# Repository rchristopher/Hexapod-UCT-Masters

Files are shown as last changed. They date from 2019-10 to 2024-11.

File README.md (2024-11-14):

# Hexapod-UCT-Masters
Hexapod project for MSc. Eng. at The University of Cape Town

#### C++ hexapod code documentation
https://rchristopher.github.io/Hexapod-UCT-Masters/

#### Final report
https://drive.google.com/file/d/1L6Y8xdj6XzMt_z8zyFrfKeZr-7HOm_jE

#### Videos of the hexapod in operation can be found at:

Hexapod Twisting its Body: https://youtu.be/Y7dhTmXj7jc

Hexapod Height Changing: https://youtu.be/q2x5ghlYeB8

Hexapod on Charging Base: https://youtu.be/d-ti27CiAhU

Hexapod Walking at Speed: https://youtu.be/vn0S7XvKXdE

Hexapod Walking on Slope: https://youtu.be/eth4lNTiyJM

Hexapod Walking with Height Changes: https://youtu.be/5solkBVhNds

Research Expo Poster

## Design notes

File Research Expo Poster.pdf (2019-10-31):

# Introduction

# Mathematical Modelling and Control System Optimization of a Hexapod Robot

## Ross Christopher Supervised by A/Prof Hennie Mouton Robotics and Agents Research Lab University of Cape Town

# Controller and Peripherals

# Mathematical Modelling

The work done in this project aims to improve the hexapod that has been developed in The University of
Cape Town’s Robotics and
Agents Research Lab, by
implementing an effective control algorithm such that the
robot can move with a
high degree of agility and precision.

The hexapod is designed to be used in search and rescue applications due to its advanced mobility.

Mathematical modelling of the robot was essential in order to develop an algorithm to achieve a smooth walking motion.

The forward kinematics of one leg was calculated using Denavit-Hartenberg notation [1] to assign coordinate systems to each joint of the leg. Using these coordinate systems a rotation matrix representing the forward kinematics was developed.

The leg joint angles were related to the foot XYZ position using inverse kinematics [2]. This was calculated with trigonometry as shown in figure 2 below.

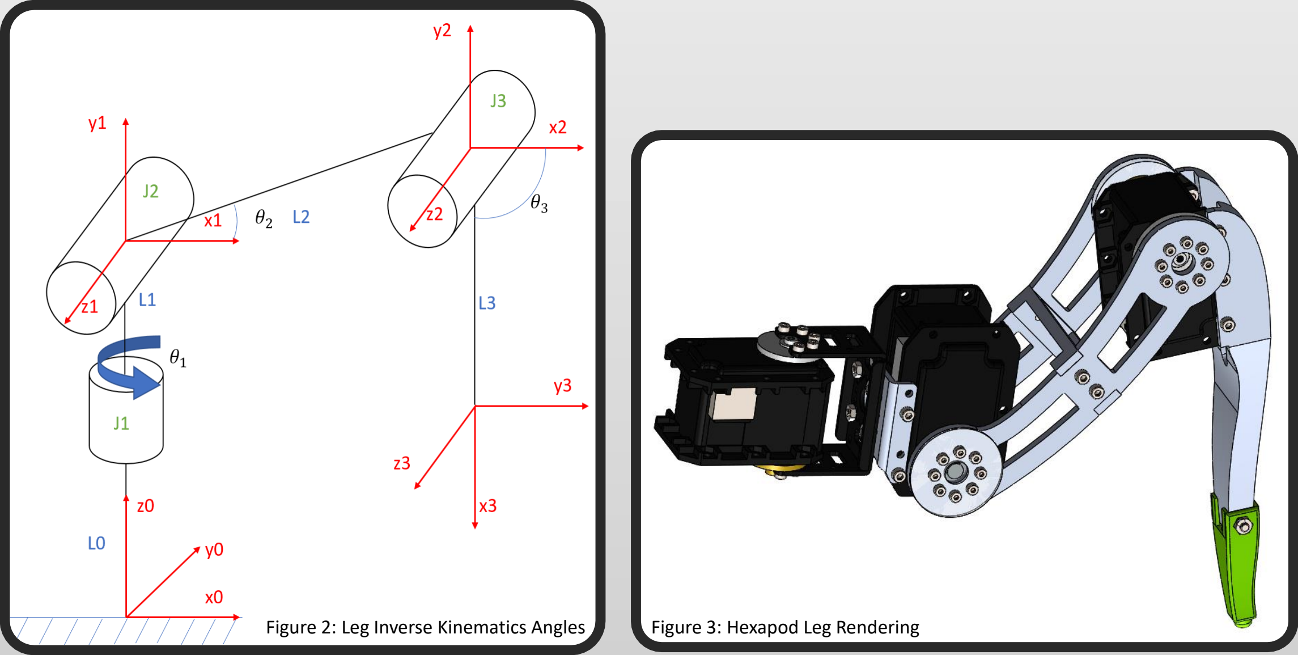
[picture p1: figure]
Figure 2: Leg Inverse Kinematics Angles; Figure 3: Hexapod Leg Rendering

This facilitated the creation of an algorithm for individual leg position control. Kinematics relating the hexapod body position to the foot position of each leg was developed.

A dynamic model for the leg was then developed using Lagrangian dynamics [3]. This model defines the relationship between joint torques and foot forces which can be used in gripping and friction force calculations.

Trajectory generation was used to generate a third order polynomial path [4] of motion for each leg; made up of the swing phase (where the leg is moving through the air) and the support phase (where the leg is touching the ground).

The hexapod includes a central microcontroller, a wireless transmitter for remote control and an accelerometer module.

An ARM microcontroller is used as the main controller of the hexapod; programmed in object orientated C++. This allows for an instant startup time of the hexapod and fast processing of commands [5]. The controller calculates the inverse kinematics of each path point, for all legs, in real time and sends this data to all 18 Dynamixel motors via serial communication.

This allows for the implementation of adaptive walking as all calculations can be adjusted and updated, in real time, as the hexapod moves.

The wireless transmitter is an RF1100-232 module. It transmits serial data between the hexapod and a computer at a speed of 433MHz. This data includes position and orientation commands from the computer and feedback signals (such as motor temperatures and torques) from the hexapod.

The accelerometer module is an XSens Mti-28A. It allows for accurate position and orientation measurement in 3 axes. These measurements are fed into a PID [6] controller which allows the orientation of the hexapod to be set and maintained. Currently the Hexapod is set to maintain a level body even if the ground is not level.

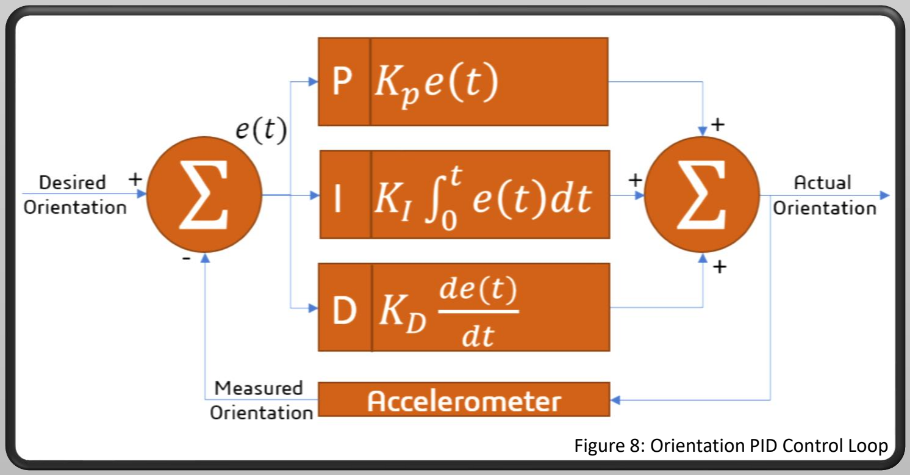
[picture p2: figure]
Figure 8: Orientation PID Control Loop

# References

### Kinematics and Dynamics

### Leg Trajectory Generation

This allows for a smooth motion when moving the foot between points as seen in the position plot in figure 4.

A tripod walking motion was achieved by moving each leg through the points in their respective paths.

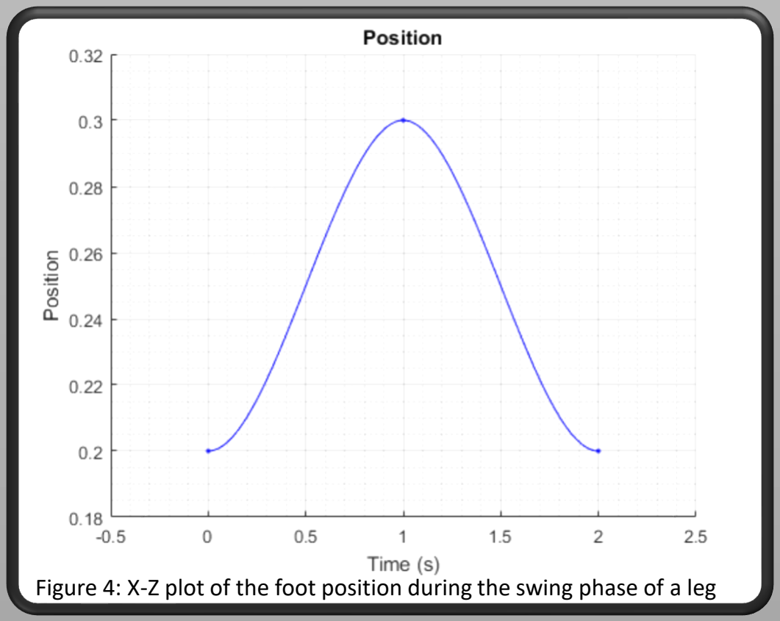
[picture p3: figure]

Figure 4: X-Z plot of the foot position during the swing phase of a leg

### STM32F4 Microcontroller

### Wireless Transmitter

Figure 6: RF1100-232 Wireless Module

Figure 5: STM32 Microcontroller Communicating with Dynamixel Motor

### Accelerometer

Figure 7: XSens Mti-28A Accelerometer

[1] A. P. Gracia, "Kinematics of Robots," 2007.
[2] M. M. U. A. a. M. A. R. Ahad, "Inverse Kinematics Solution for a 3DOF Robotic Structure using Denavit-Hartenberg Convention," 2014.
[3] T. Jintanawan, "Advanced Dynamics," 2005.
[4] C. S. Gurel, "Hexapod Modelling, Path Planning, and Control," The University of Manchester, 2017.
[5] A. Ahmed et al., "A Miniature Legged Hexapod Robot Controlled by a FPGA," International Journal of Mechanical Engineering and Mechatronics, vol. 1, no. 2, 2013.
[6] O. Aydogdu and M. Korkmaz, "A Simple Approach to Design of Variable Parameter PID controller," presented at the International Conference on Advancements in Information Technology, Singapore, 2011.

Figure 1: Hexapod Robot

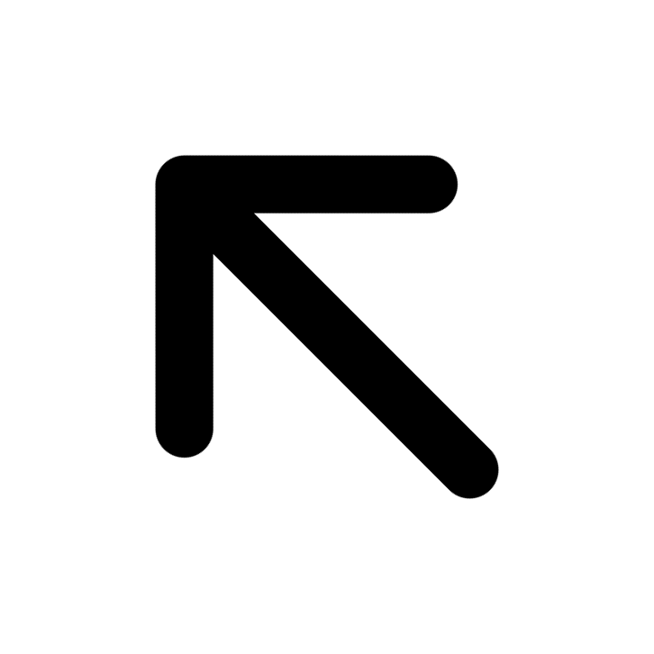
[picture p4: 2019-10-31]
Hexapod Control GUI/src/images/arrows/left_up.png

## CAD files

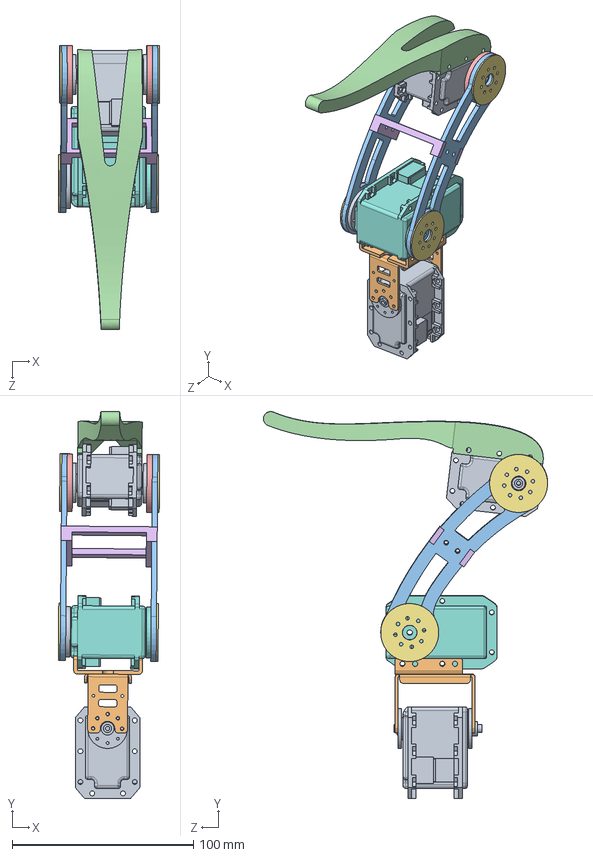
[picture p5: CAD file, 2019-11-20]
Solidworks/Assembly-Leg_no_foot.SLDASM
56.0 x 213.5 x 156.8 mm
RX-28Dual x 2
Std Part - Bracket
Leg - Femur-large x 2
Leg - Tibia - machined_no_foot
Leg - Spacer - 3mm x 2
Leg - Femur Support Bracket (large)
Leg - Spacer x 4
rx64N
RX64 bearing horn-outer
RX64 bracket (2018 new)

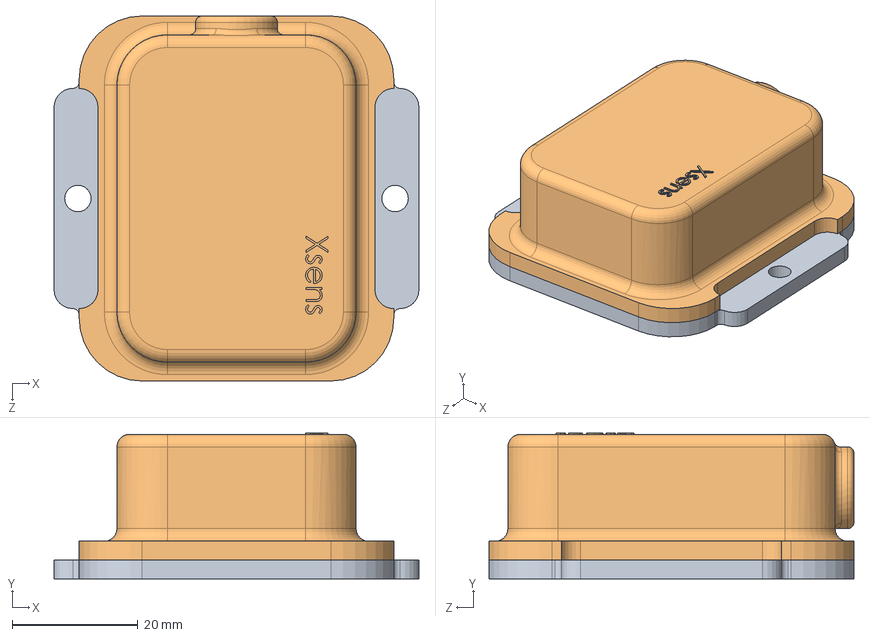
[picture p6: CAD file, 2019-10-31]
Solidworks/Xsens MTI-28/Assem8.SLDASM
58.0 x 23.2 x 58.0 mm
Base
Top

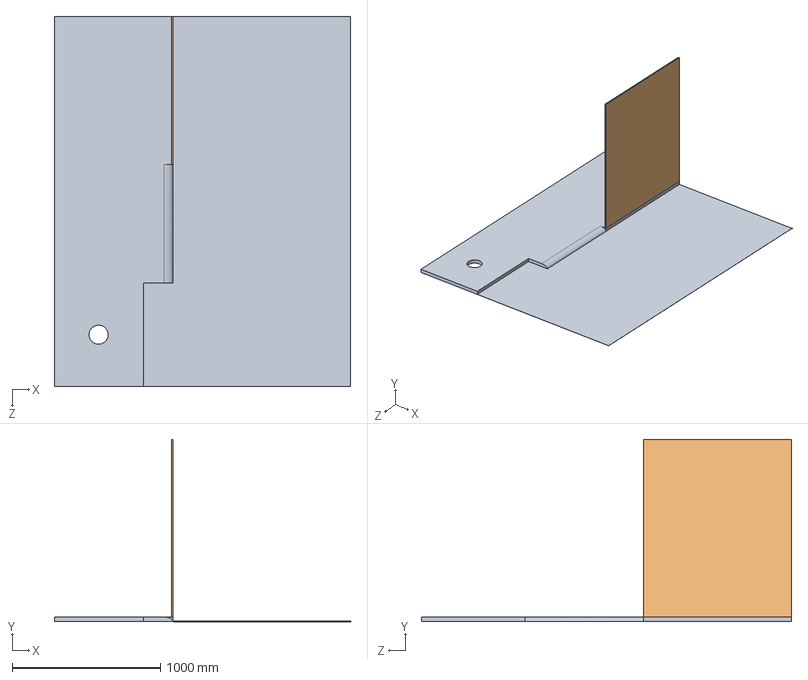
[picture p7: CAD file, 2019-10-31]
Solidworks/Assem1.SLDASM
2000.0 x 1231.0 x 2500.0 mm
Part1^Assem1
Part3^Assem1

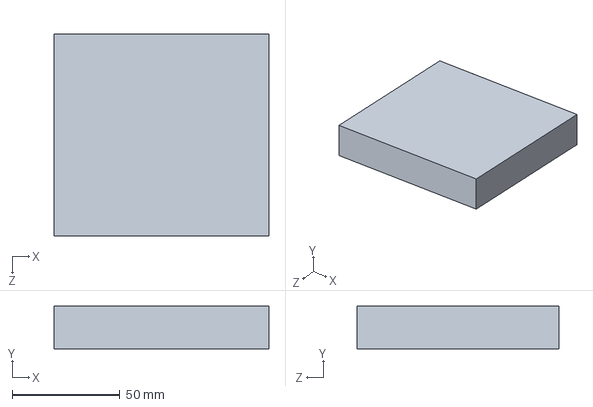
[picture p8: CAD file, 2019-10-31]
Solidworks/Circuit Boards/main prototype board.SLDPRT
100.0 x 20.0 x 94.0 mm

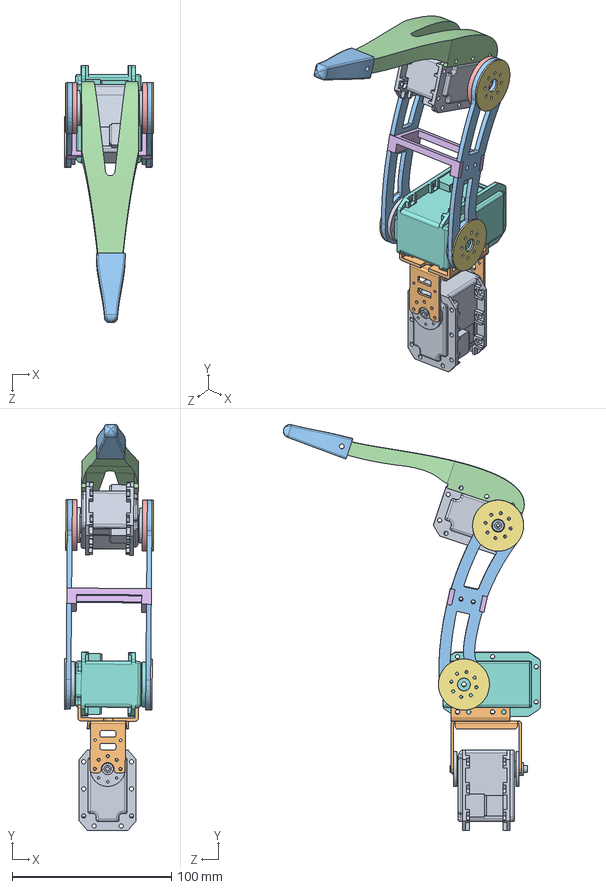
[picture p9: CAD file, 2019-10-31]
Solidworks/Assembly-Leg.SLDASM
56.1 x 254.6 x 161.3 mm
RX-28Dual x 2
Std Part - Bracket
Leg - Femur-large x 2
Leg - Tibia - machined
Leg - Spacer - 3mm x 2
Leg - Femur Support Bracket (large)
Leg - Spacer x 4
rx64N
RX64 bearing horn-outer
RX64 bracket (2018 new)
Foot_Solid_2018

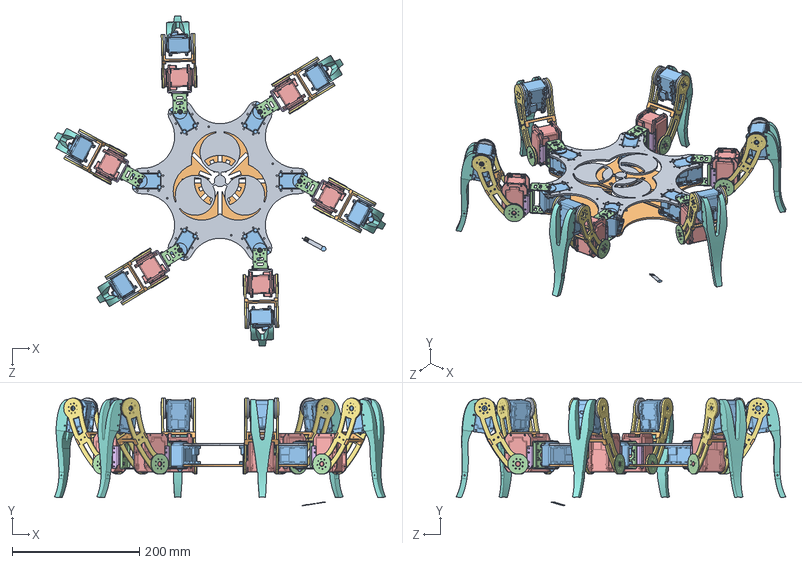
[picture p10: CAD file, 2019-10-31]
Solidworks/Assem2.SLDASM
520.1 x 169.2 x 518.3 mm
Base - Hex -upper
Base - Hex- lower
RX-28Dual x 12
Std Part - Bracket x 6
rx64H x 6
standard part - small bracket - rx64 x 6
Leg - Femur-large x 12
Leg - Tibia - machined x 6
Leg - Spacer - 2.5mm x 12
Leg - Femur Support Bracket (large) x 6
Leg - Spacer x 12

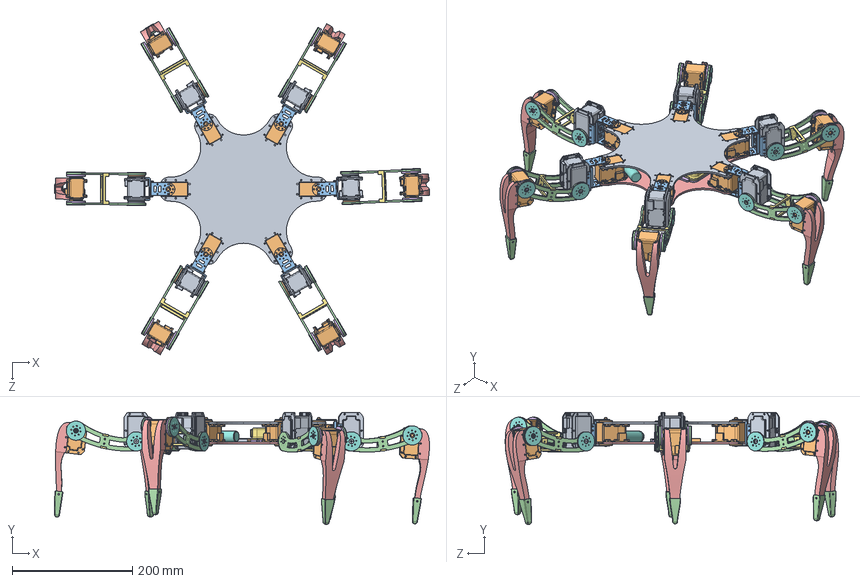
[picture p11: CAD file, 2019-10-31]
Solidworks/Assembly - Hex - 2019.SLDASM
624.0 x 186.5 x 555.0 mm
Base - Hex -upper
RX-28Dual x 12
Std Part - Bracket x 6
Leg - Femur-large x 12
Leg - Tibia - machined x 6
Leg - Spacer - 3mm x 12
Leg - Femur Support Bracket (large) x 6
Leg - Spacer x 23
rx64N x 6
RX64 bearing horn-outer x 6
RX64 bracket (2018 new) x 6
Foot_Solid_2018 x 6
Base - Hex- lower
PCB v1
remote

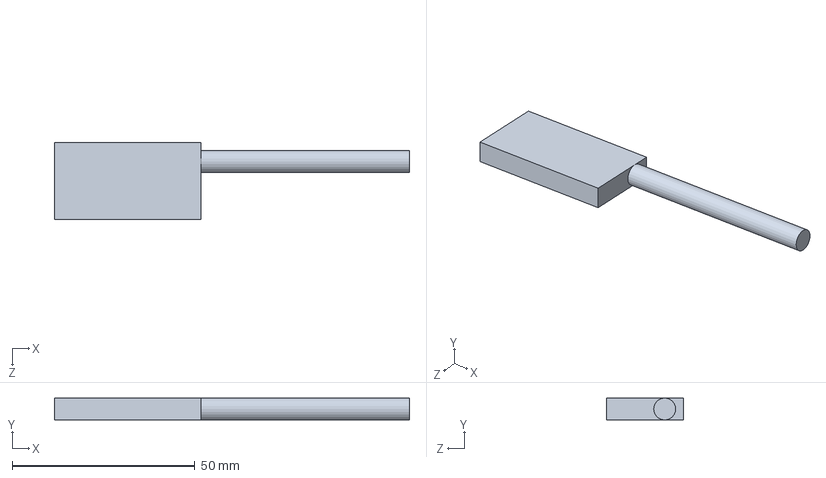
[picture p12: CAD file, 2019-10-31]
Solidworks/Circuit Boards/remote.SLDPRT
97.0 x 6.00 x 21.0 mm

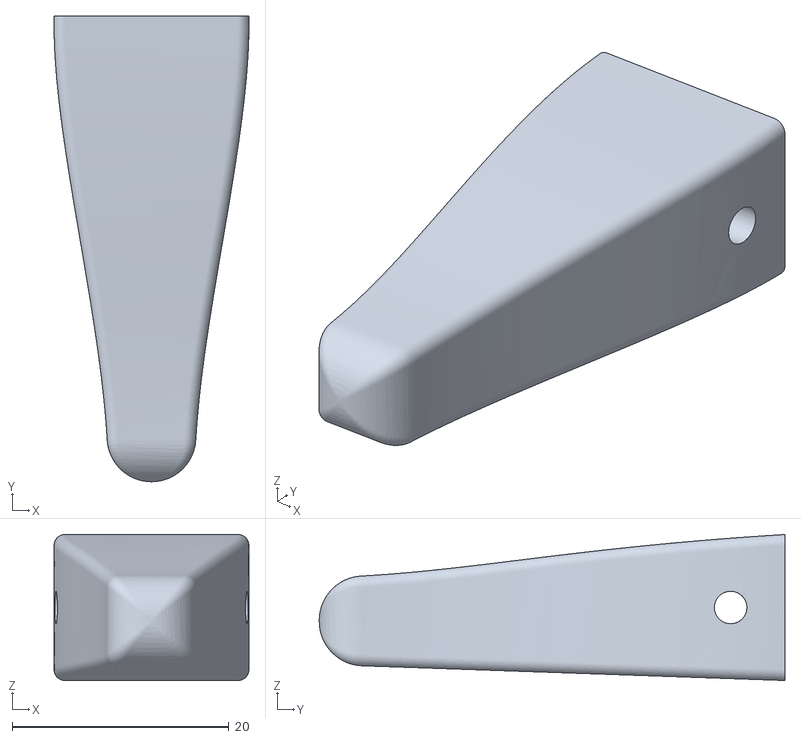
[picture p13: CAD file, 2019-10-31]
Solidworks/Parts to 3D print/Foot_Solid_2018_updated.STL
18.0 x 43.0 x 13.5

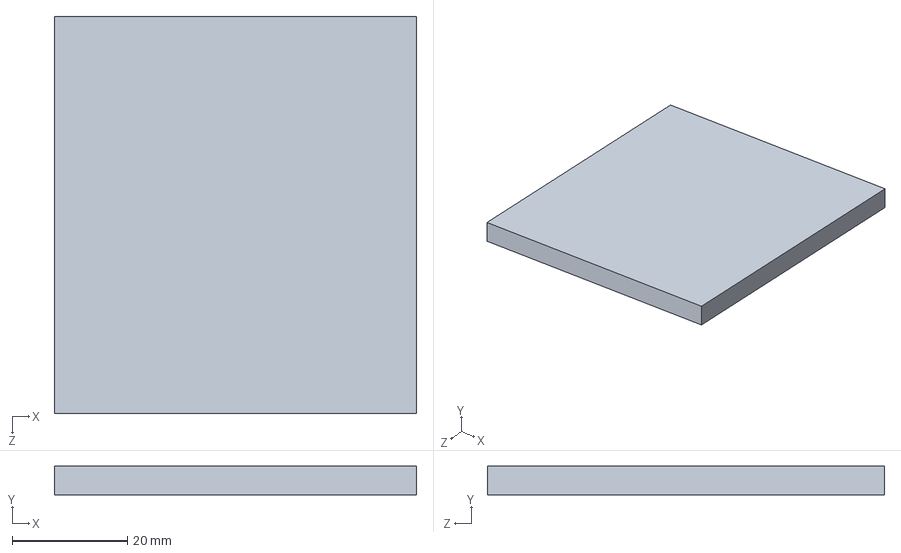
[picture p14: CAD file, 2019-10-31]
Solidworks/Circuit Boards/PCB v1.SLDPRT
63.0 x 5.00 x 69.0 mm

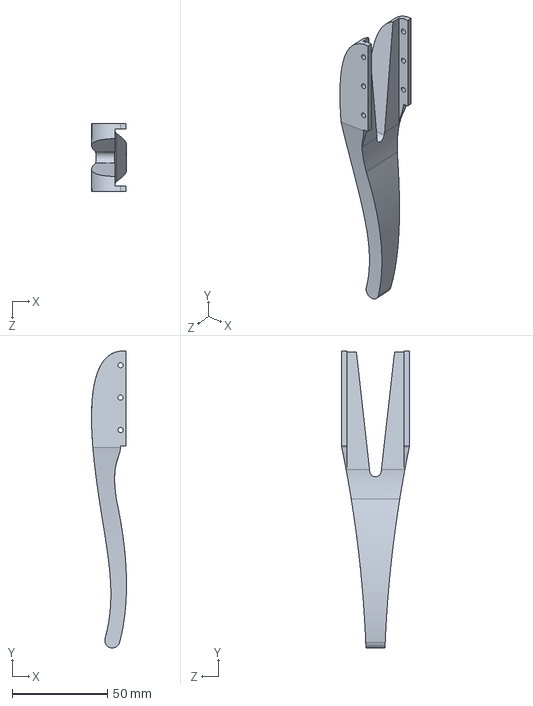
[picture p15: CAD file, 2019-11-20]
Solidworks/Leg - Tibia - machined_no_foot.SLDPRT
18.4 x 156.0 x 35.5 mm

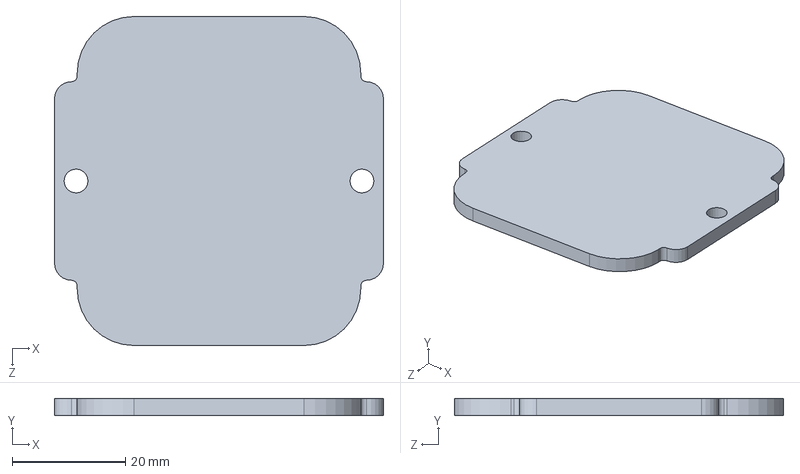
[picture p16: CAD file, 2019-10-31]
Solidworks/Xsens MTI-28/Base.SLDPRT
58.0 x 3.00 x 58.0 mm

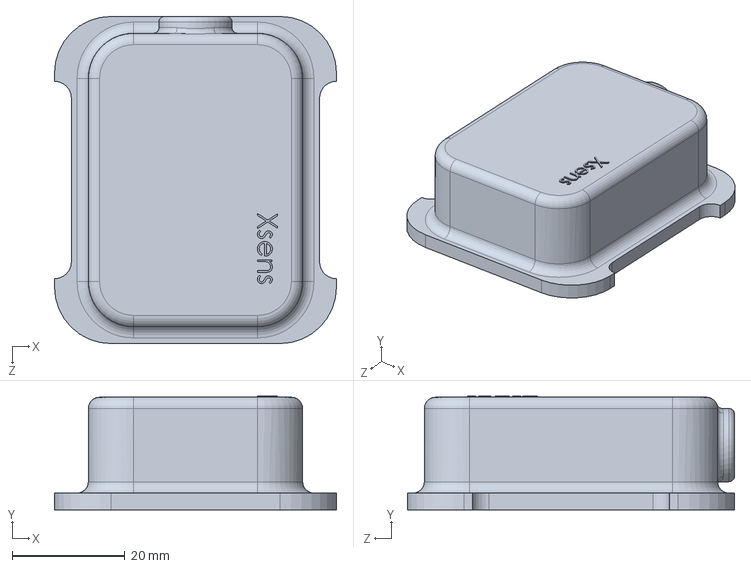
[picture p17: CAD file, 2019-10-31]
Solidworks/Xsens MTI-28/Top.SLDPRT
50.0 x 20.2 x 58.0 mm

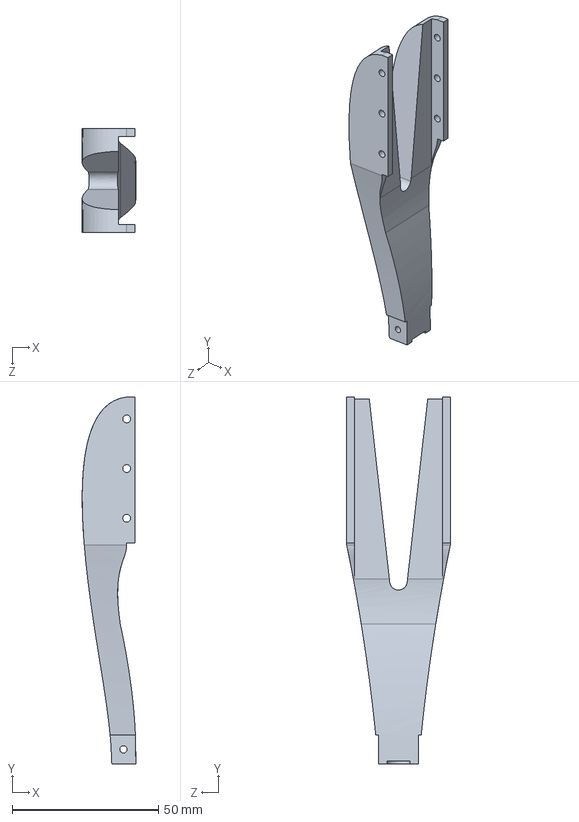
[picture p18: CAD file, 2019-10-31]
Solidworks/Leg - Tibia - machined.SLDPRT
18.4 x 125.6 x 35.5 mm

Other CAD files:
Solidworks/Std Part - Bracket.SLDPRT
Solidworks/RX-28Dual.SLDPRT
Solidworks/rx64H.SLDPRT
Solidworks/pc_mount_bar.SLDPRT
Solidworks/Assembly-Leg_old_motors.SLDASM
Solidworks/Base - Hex -upper .SLDPRT
Solidworks/Base - Hex- lower .SLDPRT
Solidworks/Circuit Protector Base.SLDPRT
Solidworks/Drawings/Protractor.SLDDRW
Solidworks/Drawings/RX64 bearing horn-outer.SLDDRW
Solidworks/Drawings/Top view base.SLDDRW
Solidworks/Drawings/rx64N_HORN.SLDDRW
Solidworks/Foot_Solid_2018.SLDPRT
Solidworks/Leg - Femur Support Bracket (large).SLDPRT
Solidworks/Leg - Femur Support Bracket.SLDPRT
Solidworks/Leg - Femur-large.SLDPRT
Solidworks/Leg - Spacer - 2.5mm (1).SLDPRT
Solidworks/Leg - Spacer - 2.5mm (2).SLDPRT
Solidworks/Leg - Spacer - 2.5mm (3).SLDPRT
Solidworks/Leg - Spacer - 2.5mm (4).SLDPRT
Solidworks/Leg - Spacer - 2.5mm.SLDPRT
Solidworks/Leg - Spacer - 3mm.SLDPRT
Solidworks/Leg - Spacer.SLDPRT
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

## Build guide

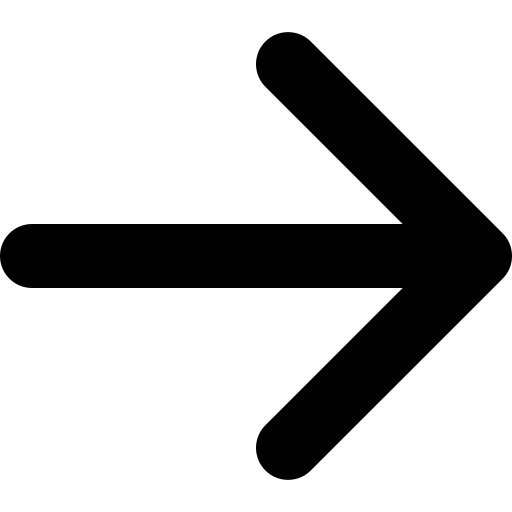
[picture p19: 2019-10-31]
Hexapod Control GUI/build/classes/images/arrows/right.png

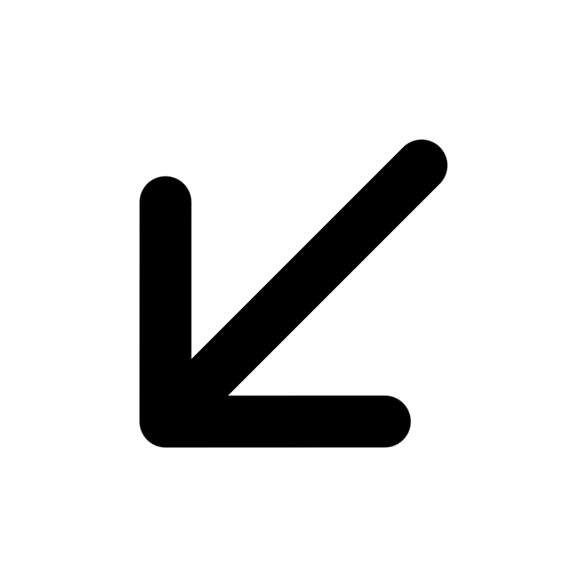
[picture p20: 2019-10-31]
Hexapod Control GUI/build/classes/images/arrows/left_down.png

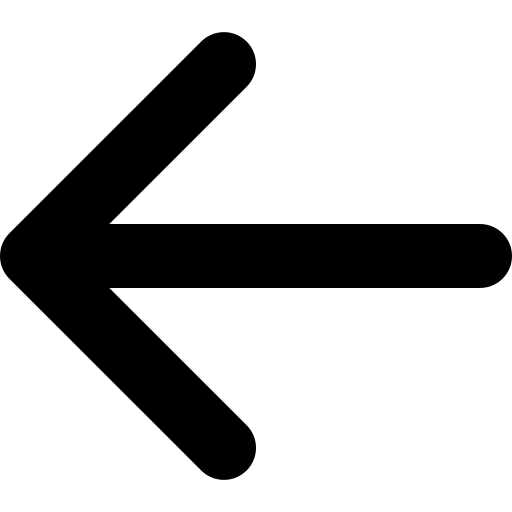
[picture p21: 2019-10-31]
Hexapod Control GUI/build/classes/images/arrows/left.png

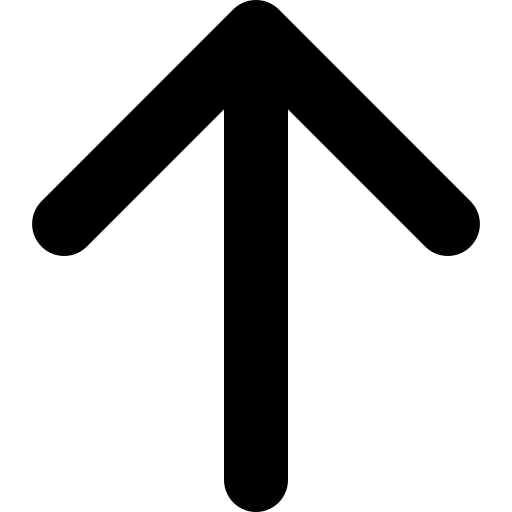
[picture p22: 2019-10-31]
Hexapod Control GUI/build/classes/images/arrows/up.png

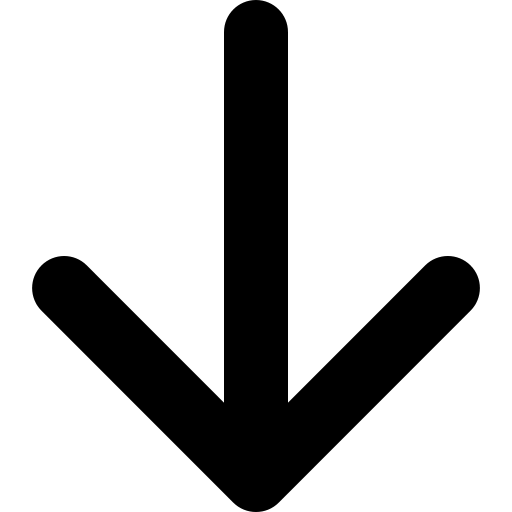
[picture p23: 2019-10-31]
Hexapod Control GUI/build/classes/images/arrows/down.png

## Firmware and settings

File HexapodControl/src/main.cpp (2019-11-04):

/**
 * @file main.cpp
 * @author Ross Christopher (CHRROS005)
 * @date
 * @brief main function
 **/

#include "CommsManager.h"
#include "Hexapod.h"

/** @brief Main Hexapod object.  **/
Hexapod HEX;

void main(){

	HEX.Initialise();
	HEX.startTimers();

	for(int i = 0; i < 1000000;i++);	//delay (HAL_Delay causes timer issues)
	HEX.stand();
	for(int i = 0; i < 100000;i++);	//delay (HAL_Delay causes timer issues)

	//HAL_Delay(5000);

	/*uint8_t data[] = {250};
	HEX.writeRegAll(RETURN_DELAY_TIME, data, 1);*/

	/*uint8_t data2[] = {32, 32};
	HEX.writeRegAll(CW_COMPLIANCE_SLOPE, data2, 2);*/

	HEX.pidPitch->togglePID(false);
	HEX.pidRoll->togglePID(false);
	HEX.pidYaw->togglePID(false);

	//HEX.pidPitch->setParameters(1,0,0);

	//uint8_t data3[] = {180,0,75,3};		//correct for motor 1 not hitting body.		// ALL IGNORING OTHER LEG POSITIONS
	//uint8_t data3[] = {75,0,245,3};		//correct for motor 2 not hitting body.
	//uint8_t data3[] = {0,0,190,3};		//correct for motor 3 not hitting body.
	/*for(int i = 0; i < 6; i++){			//change all legs
		HEX.legs[i]->motors[2]->writeReg(CW_ANGLE_LIMIT_L, data3, 4);
	}*/

	//HEX.liftOntoBase();

	HEX.timersReady = true;

	while(1){	//super loop


		/*HEX.legs[3]->setPosition(-243.710,0.0,-100);		// 1
		HEX.legs[3]->move();

		HEX.legs[3]->setPosition(-243.710,40.0,-100);	// 2
		HEX.legs[3]->move();

		HEX.legs[3]->setPosition(-243.710,-40.0,-100);	// 3
		HEX.legs[3]->move();

		HEX.legs[3]->setPosition(-283.710,0.0,-100);	// 4
		HEX.legs[3]->move();

		HEX.legs[3]->setPosition(-283.710,40.0,-100);	// 5
		HEX.legs[3]->move();

		HEX.legs[3]->setPosition(-283.710,-40.0,-100);	// 6
		HEX.legs[3]->move();

		HEX.legs[3]->setPosition(-203.710,0.0,-100);	// 7
		HEX.legs[3]->move();

		HEX.legs[3]->setPosition(-203.710,40.0,-100);	// 8
		HEX.legs[3]->move();

		HEX.legs[3]->setPosition(-203.710,-40.0,-100);	// 9
		HEX.legs[3]->move();*/

	/*	HEX.legs[3]->setPosition(-203.710,-80.0,-100);	// speed 0
		HEX.legs[3]->move();

		HEX.legs[3]->setPosition(-203.710,80.0,-100);	// speed 1
		HEX.legs[3]->move();

		HEX.legs[3]->setPosition(-203.710,0,-100);	// speed 2
		HEX.legs[3]->move();

		HEX.legs[3]->setPosition(-283.710,0,-100);	// speed 2
		HEX.legs[3]->move();

		HEX.legs[3]->setPosition(-153.710,0,-100);	// speed 3
		HEX.legs[3]->move();*/

		if(HEX.newPosition && !HEX.charging && !HEX.lowPowerMode){
			HEX.newPosition = false;

			if(HEX.direction != -10){
				HEX.setNextPathPoint();
			}

			HEX.move(DMA);
		}

	}// end super loop
}//end main

#ifdef __cplusplus
extern "C"
{
#endif		//EXTERN "C"

/**
 * @brief Timer 2 interrupt for path position control.
 *
 * @details
 **/
void TIM2_IRQHandler(void){
	HAL_TIM_IRQHandler(HEX.getTIM(TIM2));
	if(HEX.timersReady && !HEX.charging){
		if(HEX.direction != -10){
			HEX.newPosition = true;
		}
	}
}

/**
 * @brief Timer 3 interrupt for IMU and ADC reading.
 *
 * @details
 **/
void TIM3_IRQHandler(void){				// Accelerometer Reading, ADC Reading
	HAL_TIM_IRQHandler(HEX.getTIM(TIM3));
	if(HEX.timersReady){

		if((HEX.TIM3Counter % (10*(!HEX.lowPowerMode?10:20))) == 0 && HEX.TIM3Counter != 0){		//every 10 seconds if not in low power mode, 60 seconds otherwise
			struct CHARGER charger = HEX.readCharger();
			switch(charger.status){
				case FAULT:
					HEX.charging = false;
					HEX.enterLowPowerMode();
					HEX.remote->sendASCII("*****CHARGING FAULT*****");
					while(1);		//hang
					break;
				case NOT_CHARGING:
					HEX.charging = false;
					if(HEX.shouldCharging){
						HEX.startCharging();
					}
					break;
				case CHARGING_CC:
					HEX.disableMotors();
					HEX.charging = true;
					break;
				case CHARGING_CV:
					HEX.disableMotors();
					HEX.charging = true;
					break;
				default:
					break;
			}

			if(charger.voltage <= 20.0 && charger.voltage > 10.0){
				HEX.remote->sendASCII("LOW BATTERY");
				HEX.lowBatteryCount++;

				if(HEX.lowBatteryCount >= 6){	//make sure that battery is actually low and not just a spike by checking for 1 minute.
					if(!HEX.lowPowerMode){
						HEX.enterLowPowerMode();
					}
					if(NOT_CHARGING){
						HEX.shouldCharging = true;
						HEX.startCharging();
					}
				}
			}else{
				HEX.lowBatteryCount = 0;
				if(HEX.lowPowerMode){
					HEX.exitLowPowerMode();
				}
			}

			uint8_t data[10] = {255, 249, charger.status, 0,0,0,0, 0,0,0};
			HEX.remote->floatToBytes(charger.voltage, &data[3]);
			long checksumTemp = 0;
			for(int i = 0; i < 9; i++){
				checksumTemp += data[i];
			}
			data[9] = (uint8_t)checksumTemp;

			HEX.remote->sending = false;
			if(!HEX.remote->sending){
				HEX.remote->sending = true;
				HEX.comms.transmitRemote(data, 10, 100, DMA);
			}

			//HEX.TIM3Counter = 0;
		}

		/*if((HEX.TIM3Counter % (200*10)) == 0){		//every 10 seconds
			//HEX.readInternalTemp();
			if((HEX.currentTemperature - HEX.startingTemperature)*(HEX.currentTemperature - HEX.startingTemperature) > 40.0*40.0 || HEX.currentTemperature > 120.0){
				//HEX.fullSystemReset(true);	//over-heating (also add battery shutdown/motor shutdown)
			}
		}*/

		// PING COMPUTER
		if((HEX.TIM3Counter % (10*5)) == 0 && HEX.TIM3Counter != 0 && !HEX.lowPowerMode){	//every 5 seconds, brackets around (10*time) are important!
			if (HEX.remote->pingSuccess) {
				HEX.remote->pingSuccess = false;
				uint8_t data[2] = {255, 250};
				HEX.remote->sending = true;
				HEX.comms.transmitRemote(data, 2, 100, DMA);
				HEX.comms.remoteFailureCount = 0;
			} else {
				//trace_printf("COMMS FAILURE\n");
				//HEX.remote->sendASCII("COMMS FAILURE");
				if (HEX.comms.remoteFailureCount >= 10) {
					HEX.stop();
					HEX.comms.remoteFailureCount = 0;
					//HEX.remote->sendASCII("RESETTING...");
					//trace_printf("RESETTING...\n");
					//HEX.fullSystemReset(true);
				} else {
					HEX.comms.remoteFailureCount++;
				}
			}
		}


		if((HEX.TIM3Counter % (uint8_t)(10*HEX.IMUTransFreq)) == 0 && HEX.TIM3Counter != 0 && !HEX.charging && !HEX.lowPowerMode){	//every 1 seconds, brackets around (10*time) are important!
			HEX.remote->sending = false;
			if(!HEX.remote->sending){
				HEX.remote->sending = true;
				HEX.remote->sendAcc(HEX.accel->pitch, HEX.accel->roll, HEX.accel->yaw, HEX.accel->timestamp, HEX.slopePitch, HEX.slopeRoll);
			}
		}

		if(!HEX.shouldCharging && !HEX.lowPowerMode){
			HEX.accel->requestAccelData();
		}


		HEX.TIM3Counter++;

	}
}

/**
 * @brief UART transmit complete interrupt.
 *
 * @details
 *
 * @param UART_HandleStructure Pointer to the UART struct which caused the error interrupt.
 **/
void HAL_UART_TxCpltCallback(UART_HandleTypeDef * UART_HandleStructure){
	__HAL_UART_CLEAR_FLAG(UART_HandleStructure, UART_FLAG_TC);
	//__HAL_UART_CLEAR_OREFLAG(UART_HandleStructure);

	UART_HandleStructure->gState = HAL_UART_STATE_READY;

	if(UART_HandleStructure->Instance == UART3){
		//accelerometer transmit complete
	}else if(UART_HandleStructure->Instance == UART2){
		//remote transmit complete
		if(UART_HandleStructure->pTxBuffPtr[0]==255 && UART_HandleStructure->pTxBuffPtr[1]==248 && (UART_HandleStructure->pTxBuffPtr[9]==252 || UART_HandleStructure->pTxBuffPtr[9]==253 ) ){
			//HEX.remote->sendCharging(HEX.shouldCharging);
		}
	}else if(UART_HandleStructure->Instance == UART1){
		//HEX.UART1_Toggle_Read();
	}
}

/**
 * @brief UART receive complete interrupt.
 *
 * @details
 *
 * @param UART_HandleStructure Pointer to the UART struct which caused the error interrupt.
 **/
void HAL_UART_RxCpltCallback(UART_HandleTypeDef * UART_HandleStructure){
	__HAL_UART_CLEAR_FLAG(UART_HandleStructure, UART_FLAG_RXNE);
	//__HAL_UART_CLEAR_OREFLAG(UART_HandleStructure);

	UART_HandleStructure->RxState = HAL_UART_STATE_READY;
	UART_HandleStructure->gState = HAL_UART_STATE_READY;

	if(UART_HandleStructure->Instance == UART1){

	}else if(UART_HandleStructure->Instance == UART2){						//remote data
		if(UART_HandleStructure->pRxBuffPtr[0] == 0x01 && UART_HandleStructure->pRxBuffPtr[7] == 0x04){	//remote movement data
			HEX.remote->processRemoteData();
			HEX.update();
		}else if(UART_HandleStructure->pRxBuffPtr[0] == 55){	//remote ping data
			HEX.remote->pingSuccess = true;
		}else if(UART_HandleStructure->pRxBuffPtr[0] == 255 && UART_HandleStructure->pRxBuffPtr[1] == 248){	//BASE TO HEXAPOD
			if(UART_HandleStructure->pRxBuffPtr[2] == 55){	//command incoming
				if(UART_HandleStructure->pRxBuffPtr[3] == 1){	//start charging
					HEX.shouldCharging = true;
					HEX.startCharging();
				}else if(UART_HandleStructure->pRxBuffPtr[3] == 0){	//stop charging
					HEX.shouldCharging = false;
					HEX.stopCharging();
				}
			}else{
				// status and voltage incoming
			}
		}else if(UART_HandleStructure->pRxBuffPtr[0] == 255 && UART_HandleStructure->pRxBuffPtr[1] == 250){// toggle motors command
			bool toggleMotors = (bool)UART_HandleStructure->pRxBuffPtr[2];
			switch(toggleMotors){
				case 0:
					HEX.disableMotors();
					break;
				case 1:
					HEX.enableMotors();
					break;
				default: break;
			}
		}else if(UART_HandleStructure->pRxBuffPtr[0] == 255 && UART_HandleStructure->pRxBuffPtr[1] == 251){	//disable/enable pitch/roll PID
			bool togglePID = (bool)UART_HandleStructure->pRxBuffPtr[2];
			uint8_t pitchRoll = UART_HandleStructure->pRxBuffPtr[3];

			if(!HEX.liftedForBase){
				if(pitchRoll == 1){	//pitch
					HEX.pidPitch->togglePID(togglePID);
				}else if(pitchRoll == 2){	// roll
					HEX.pidRoll->togglePID(togglePID);
				}else if(pitchRoll == 3){
					HEX.pidPitch->togglePID(togglePID);
					HEX.pidRoll->togglePID(togglePID);
				}
			}
		}else if(UART_HandleStructure->pRxBuffPtr[0] == 255 && UART_HandleStructure->pRxBuffPtr[1] == 222){ // set PID parameters command
				if(UART_HandleStructure->pRxBuffPtr[2] == 1){//pitch
					if(UART_HandleStructure->pRxBuffPtr[3]==1){//kp
						HEX.pidPitch->setKp(HEX.remote->bytesToFloat(&UART_HandleStructure->pRxBuffPtr[4]));
					}else if(UART_HandleStructure->pRxBuffPtr[3]==2){//ki
						HEX.pidPitch->setKi(HEX.remote->bytesToFloat(&UART_HandleStructure->pRxBuffPtr[4]));
					}else if(UART_HandleStructure->pRxBuffPtr[3]==3){//kd
						HEX.pidPitch->setKd(HEX.remote->bytesToFloat(&UART_HandleStructure->pRxBuffPtr[4]));
					}
				}else if(UART_HandleStructure->pRxBuffPtr[2] == 2){//roll
					if(UART_HandleStructure->pRxBuffPtr[3]==1){//kp
						HEX.pidRoll->setKp(HEX.remote->bytesToFloat(&UART_HandleStructure->pRxBuffPtr[4]));
					}else if(UART_HandleStructure->pRxBuffPtr[3]==2){//ki
						HEX.pidRoll->setKi(HEX.remote->bytesToFloat(&UART_HandleStructure->pRxBuffPtr[4]));
					}else if(UART_HandleStructure->pRxBuffPtr[3]==3){//kd
						HEX.pidRoll->setKd(HEX.remote->bytesToFloat(&UART_HandleStructure->pRxBuffPtr[4]));
						for(int i = 0; i < 1; i++);
					}
				}else if(UART_HandleStructure->pRxBuffPtr[2] == 3){//both
					if(UART_HandleStructure->pRxBuffPtr[3]==1){//kp
						HEX.pidPitch->setKp(HEX.remote->bytesToFloat(&UART_HandleStructure->pRxBuffPtr[4]));
						HEX.pidRoll->setKp(HEX.remote->bytesToFloat(&UART_HandleStructure->pRxBuffPtr[4]));
					}else if(UART_HandleStructure->pRxBuffPtr[3]==2){//ki
						HEX.pidPitch->setKi(HEX.remote->bytesToFloat(&UART_HandleStructure->pRxBuffPtr[4]));
						HEX.pidRoll->setKi(HEX.remote->bytesToFloat(&UART_HandleStructure->pRxBuffPtr[4]));
					}else if(UART_HandleStructure->pRxBuffPtr[3]==3){//kd
						HEX.pidPitch->setKd(HEX.remote->bytesToFloat(&UART_HandleStructure->pRxBuffPtr[4]));
						HEX.pidRoll->setKd(HEX.remote->bytesToFloat(&UART_HandleStructure->pRxBuffPtr[4]));
						for(int i = 0; i < 1; i++);
					}
				}
		}else if(UART_HandleStructure->pRxBuffPtr[0] == 255 && UART_HandleStructure->pRxBuffPtr[1] == 221){ // set IMU transmission frequency
			HEX.IMUTransFreq = HEX.remote->bytesToFloat(&UART_HandleStructure->pRxBuffPtr[2]);
		}

	}else if(UART_HandleStructure->Instance == UART3){							//accelerometer data

		if(UART_HandleStructure->pRxBuffPtr[0] == 255 && UART_HandleStructure->pRxBuffPtr[1]){	//ping command

		}else{

			HEX.accel->processAccelData();

			if(HEX.pidPitch->enabled || HEX.pidRoll->enabled){

				double pitch = HEX.pidPitch->calculate(HEX.pitchSetPoint, HEX.accel->pitch);	//if disabled it returns the set point (zero in most cases).
				double roll = HEX.pidRoll->calculate(HEX.rollSetPoint, HEX.accel->roll);

				double angleLimit = 0.6; //34.3775 degrees

				if( (pitch < angleLimit) && (pitch > -angleLimit) && (roll < angleLimit) && (roll > -angleLimit) ){

					HEX.setPose(roll, pitch);
					if(HEX.direction == -10){
						HEX.newPosition = true;
					}

				}else{

					if((pitch > angleLimit) || (pitch < -angleLimit)){
						//HEX.pidPitch->reset();
						//HEX.pidPitch->setParameters(-1.05, -2.2, 0);
					}
					if((roll > angleLimit) || (roll < -angleLimit)){
						//HEX.pidRoll->reset();
						//HEX.pidRoll->setParameters(-1.05, -2.2, 0);
					}

					if(HEX.direction == -10){
						//HEX.newPosition = true;
					}

				}

			}

			/*if(HEX.pidYaw->enabled){

				double yaw = HEX.pidYaw->calculate(HEX.yawSetPoint, HEX.accel->yaw);

				if(yaw <= 1 && yaw >= -1){
					//HEX.twistBody(yaw);
				}else{
					for(int i = 0; (i*i) < (yaw*yaw)*2; i++){
						//HEX.turnBody(yaw < 0 ? -0.5 : 0.5, ABSOLUTE);
					}
					//HEX.twistBody(0);
				}
			}*/
		}
	}
}

/**
 * @brief UART Error Handler
 *
 * @details
 *
 * @param UART_HandleStructure Pointer to the UART struct which caused the error interrupt.
 **/
void HAL_UART_ErrorCallback(UART_HandleTypeDef * UART_HandleStructure){
	uint32_t error = 0;
	uint8_t errorLoc = 0;

	__HAL_UNLOCK(UART_HandleStructure);

	__HAL_UART_CLEAR_FLAG(UART_HandleStructure, UART_FLAG_RXNE);
	__HAL_UART_CLEAR_FLAG(UART_HandleStructure, UART_FLAG_TC);

	if(UART_HandleStructure->Instance == UART1){
		//trace_printf("UART ERROR (%s): ", "UART1");
		errorLoc = 1;
	}else if(UART_HandleStructure->Instance == UART2){
		//trace_printf("UART ERROR (%s): ", "UART2");
		errorLoc = 2;
	}else if(UART_HandleStructure->Instance == UART3){
		//trace_printf("UART ERROR (%s): ", "UART3");
		errorLoc = 3;
	}

	switch(UART_HandleStructure->ErrorCode){
		case HAL_UART_ERROR_NONE:
			break;
		case HAL_UART_ERROR_DMA:
			error = HAL_UART_ERROR_DMA;
			//trace_printf("DMA transfer error");
			break;
		case HAL_UART_ERROR_FE:
			error = HAL_UART_ERROR_FE;
			__HAL_UART_CLEAR_FEFLAG(UART_HandleStructure);
			//trace_printf("Frame error");
			break;
		case HAL_UART_ERROR_NE:
			error = HAL_UART_ERROR_NE;
			__HAL_UART_CLEAR_NEFLAG(UART_HandleStructure);
			//trace_printf("Noise error");
			break;
		case HAL_UART_ERROR_ORE:
			error = HAL_UART_ERROR_ORE;
			__HAL_UART_CLEAR_OREFLAG(UART_HandleStructure);
			//trace_printf("Overrun error");
			break;
		case HAL_UART_ERROR_PE:
			error = HAL_UART_ERROR_PE;
			__HAL_UART_CLEAR_PEFLAG(UART_HandleStructure);
			//trace_printf("Parity error");
			break;
	}

	//trace_printf("\n");

	__HAL_UART_FLUSH_DRREGISTER(UART_HandleStructure);
	UART_HandleStructure->ErrorCode = 0;

	//__HAL_DMA_ENABLE(UART_HandleStructure->hdmarx);
	//__HAL_DMA_ENABLE(UART_HandleStructure->hdmatx);
	__HAL_UART_ENABLE(UART_HandleStructure);

	UART_HandleStructure->gState = HAL_UART_STATE_READY;
	UART_HandleStructure->RxState = HAL_UART_STATE_READY;

	if(errorLoc == 1){
		HEX.direction = -10;
		HEX.newPosition = false;
	}else if(errorLoc == 2 && !HEX.lowPowerMode){	//remote error
		HEX.remote->receiveRemoteData(10);
	}

	HEX.remote->sending = false;
	if(!HEX.lowPowerMode){
		HEX.remote->sendError(errorLoc, error);
	}
	HEX.remote->sending = false;
	//HEX._Error_Handler(__FILE__, __LINE__);		//hangs in infinite while loop
}

/** UNUSED IN DMA MODE, but needed or else code hangs **/
/**
 * @brief UART1 (Motor) Handler.
 *
 * @details
 **/
void USART1_IRQHandler(void){HAL_UART_IRQHandler(HEX.comms.getMotorUART());}

/**
 * @brief UART2 (Remote) Handler.
 *
 * @details
 **/
void USART2_IRQHandler(void){
	HAL_UART_IRQHandler(HEX.comms.getRemoteUART());
}

/**
 * @brief UART3 (IMU) Handler.
 *
 * @details
 **/
void USART3_IRQHandler(void){HAL_UART_IRQHandler(HEX.comms.getAccUART());}
/*********/

/** DMA INTERRUPTS (Runs before read/write) **/
/**
 * @brief Motor (UART1) TX DMA Handler.
 *
 * @details
 **/
void DMA2_Stream7_IRQHandler(void){
	HAL_DMA_IRQHandler(HEX.comms.getMotorDMA(TX));}

/**
 * @brief Motor (UART1) RX DMA Handler.
 *
 * @details
 **/
void DMA2_Stream2_IRQHandler(void){
	HAL_DMA_IRQHandler(HEX.comms.getMotorDMA(RX));}

/**
 * @brief Remote (UART2) TX DMA Handler.
 *
 * @details
 **/
void DMA1_Stream6_IRQHandler(void){
	HAL_DMA_IRQHandler(HEX.comms.getRemoteDMA(TX));
}

/**
 * @brief Remote (UART2) RX DMA Handler.
 *
 * @details
 **/
void DMA1_Stream5_IRQHandler(void){
	HAL_DMA_IRQHandler(HEX.comms.getRemoteDMA(RX));}

/**
 * @brief IMU (UART3) TX DMA Handler.
 *
 * @details
 **/
void DMA1_Stream3_IRQHandler(void){
	HAL_DMA_IRQHandler(HEX.comms.getAccDMA(TX));}

/**
 * @brief IMU (UART3) RX DMA Handler.
 *
 * @details
 **/
void DMA1_Stream1_IRQHandler(void){
	HAL_DMA_IRQHandler(HEX.comms.getAccDMA(RX));}
/*********/

/**
 * @brief Systick Handler.
 *
 * @details
 **/
void SysTick_Handler(void) {
	HAL_IncTick();
}

#ifdef __cplusplus
}
#endif //EXTERN "C"

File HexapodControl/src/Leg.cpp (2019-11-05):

/**
 * @file Leg.cpp
 * @author Ross Christopher (CHRROS005)
 * @date
 * @brief Leg class functions.
 **/

#include "Leg.h"

Leg::Leg(CommsManager * comms){
	this->comms = comms;
	this->motors[0] = NULL;
	this->motors[1] = NULL;
	this->motors[2] = NULL;
	this->rotation = 0;
}

Leg::Leg(Motor m1, Motor m2, Motor m3, uint16_t rotation, double duty_offset, CommsManager * comms){

	this->comms = comms;

	this->motors[0] = new Motor(m1);
	this->motors[1] = new Motor(m2);
	this->motors[2] = new Motor(m3);

	this->positionTHETA.p1 = 0;
	this->positionTHETA.p2 = 0;
	this->positionTHETA.p3 = 0;

	this->theta_dot->p1 = 0;
	this->theta_dot->p2 = 0;
	this->theta_dot->p3 = 0;

	this->positionXYZ.p1 = 0;
	this->positionXYZ.p2 = 0;
	this->positionXYZ.p3 = 0;

	this->rotation = rotation;

	this->dutyOffset = duty_offset;
}

Leg::Leg(uint8_t ID1, uint8_t ID2, uint8_t ID3, uint16_t rotation, double duty_offset, CommsManager * comms){

	this->comms = comms;

	this->motors[0] = new Motor(ID1, comms);
	this->motors[1] = new Motor(ID2, comms);
	this->motors[2] = new Motor(ID3, comms);

	this->positionTHETA.p1 = 0;
	this->positionTHETA.p2 = 0;
	this->positionTHETA.p3 = 0;

	this->theta_dot->p1 = 0;
	this->theta_dot->p2 = 0;
	this->theta_dot->p3 = 0;

	this->positionXYZ.p1 = 0;
	this->positionXYZ.p2 = 0;
	this->positionXYZ.p3 = 0;

	this->rotation = rotation;

	this->dutyOffset = duty_offset;

	this->currentPathPoint = (this->legPath->pathSize*2-1)*duty_offset;	//x*duty_offset.... x is numPointsDef+pathSizeDef from Path.h

}

Leg::~Leg(void){

}

void Leg::setOffsets(double off1, double off2, double off3){
	this->offsets.p1 = off1;
	this->offsets.p2 = off2;
	this->offsets.p3 = off3;
}

void Leg::setPosition(double x, double y, double z){
	this->positionXYZ.p1 = x;
	this->positionXYZ.p2 = y;
	this->positionXYZ.p3 = z;

	this->inverseKinematics();
	this->setPositionBits();
}


void Leg::setPosition(double * xyz){
	this->positionXYZ.p1 = xyz[0];
	this->positionXYZ.p2 = xyz[1];
	this->positionXYZ.p3 = xyz[2];

	this->inverseKinematics();
	this->setPositionBits();

	//this->forwardKinematics();
}

void Leg::setTheta(double theta1, double theta2, double theta3){
	this->positionTHETA.p1 = theta1;
	this->positionTHETA.p2 = theta2;
	this->positionTHETA.p3 = theta3;

	this->forwardKinematics();
	this->setPositionBits();
}

void Leg::setTheta(double * theta){
	this->positionTHETA.p1 = theta[0];
	this->positionTHETA.p2 = theta[1];
	this->positionTHETA.p3 = theta[2];

	this->forwardKinematics();
	this->setPositionBits();
}


double Leg::Lib_abs(double val){
	if(val < 0){
		return val*(-1);
	}else{
		return val;
	}
}

void Leg::setSpeed(double _xd, double _yd, double _zd){

	double th1 = this->positionTHETA.p1;	//radians
	double th2 = this->positionTHETA.p2;
	double th3 = this->positionTHETA.p3;

	double xd_global = (_xd/1000.0);	//m/s		// global coords
	double yd_global = (_yd/1000.0);
	double zd_global = (_zd/1000.0);

	const double LEG = (double)(this->rotation)*M_PI/180.0;
	double xd = (xd_global)*cos(LEG) - (yd_global+0.0)*sin(LEG);
	double yd = (yd_global)*cos(LEG) + (xd_global+0.0)*sin(LEG);
	double zd = zd_global;

	/*if(th3 == 0){
		th3 = 0.1;
	}*/

	L1x *= 0.001;
	L1z *= 0.001;
	L2 *= 0.001;
	L3 *= 0.001;

	double _thd1 =  (yd*cos(th1) - xd*sin(th1))/(L1x + L3*cos(th2 + th3) + L2*cos(th2)) ;	//correct

	double _thd2 = (1/L2)*( zd*cos(th2) - xd*cos(th1)*sin(th2) - yd*sin(th1)*sin(th2) + ((cos(th3))/(sin(th3)))*(zd*sin(th2) + xd*cos(th1)*cos(th2) + yd*cos(th2)*sin(th1)) );// (zd*cos(th2))/L2 - (xd*cos(th1)*sin(th2))/L2 - (yd*sin(th1)*sin(th2))/L2 + (L3*L3*zd*cos(th3)*sin(th2)*sin(th3))/(- L2*L3*L3*cos(th3)*cos(th3) + L2*L3*L3 + L2 + L2*cos(th1)) + (L3*L3*xd*cos(th1)*cos(th2)*cos(th3)*sin(th3))/(- L2*L3*L3*cos(th3)*cos(th3) + L2*L3*L3 + L2 + L2*cos(th1)) + (L3*L3*yd*cos(th2)*cos(th3)*sin(th1)*sin(th3))/(- L2*L3*L3*cos(th3)*cos(th3) + L2*L3*L3 + L2 + L2*cos(th1));
			//(zd*sin(th2 + th3) + xd*cos(th2 + th3)*cos(th1) + yd*cos(th2 + th3)*sin(th1))/(L2*0.001*sin(th3));//old

	double _thd3 = -(1/L2)*( zd*cos(th2) - xd*cos(th1)*sin(th2) - yd*sin(th1)*sin(th2) + (L2 + L3*(cos(th3))/(L3*sin(th3)))*(zd*sin(th2) + xd*cos(th1)*cos(th2) + yd*cos(th2)*sin(th1)) );// (zd*cos(th2))/L2 - (xd*cos(th1)*sin(th2))/L2 - (yd*sin(th1)*sin(th2))/L2 + (L3*L3*zd*cos(th3)*sin(th2)*sin(th3))/(- L2*L3*L3*cos(th3)*cos(th3) + L2*L3*L3 + L2 + L2*cos(th1)) + (L3*L3*xd*cos(th1)*cos(th2)*cos(th3)*sin(th3))/(- L2*L3*L3*cos(th3)*cos(th3) + L2*L3*L3 + L2 + L2*cos(th1)) + (L3*L3*yd*cos(th2)*cos(th3)*sin(th1)*sin(th3))/(- L2*L3*L3*cos(th3)*cos(th3) + L2*L3*L3 + L2 + L2*cos(th1));;
	//-(zd*cos(th2) + L3*L3*zd*cos(th2) + zd*cos(th1)*cos(th2) - xd*cos(th1)*sin(th2) - yd*sin(th1)*sin(th2) - xd*cos(th1)*cos(th1)*sin(th2) - L3*L3*xd*cos(th1)*sin(th2) - L3*L3*yd*sin(th1)*sin(th2) - yd*cos(th1)*sin(th1)*sin(th2) - L3*L3*zd*cos(th2)*cos(th3)*cos(th3) + L3*L3*zd*cos(th3)*sin(th2)*sin(th3) + L2*L3*zd*sin(th2)*sin(th3) + L3*L3*xd*cos(th1)*cos(th3)*cos(th3)*sin(th2) + L3*L3*yd*cos(th3)*cos(th3)*sin(th1)*sin(th2) + L3*L3*yd*cos(th2)*cos(th3)*sin(th1)*sin(th3) + L2*L3*xd*cos(th1)*cos(th2)*sin(th3) + L2*L3*yd*cos(th2)*sin(th1)*sin(th3) + L3*L3*xd*cos(th1)*cos(th2)*cos(th3)*sin(th3))/(L2*(- L3*L3*cos(th3)*cos(th3) + L3*L3 + cos(th1) + 1));
			//-(zd*(L3*0.001*sin(th2 + th3) + L2*0.001*sin(th2)))/(L2*0.001*L3*0.001*sin(th3)) - (xd*cos(th1)*(L3*0.001*cos(th2 + th3) + L2*0.001*cos(th2)))/(L2*0.001*L3*0.001*sin(th3)) - (yd*sin(th1)*(L3*0.001*cos(th2 + th3) + L2*0.001*cos(th2)))/(L2*0.001*L3*0.001*sin(th3)) ;//old

	L1x /= 0.001;
	L1z /= 0.001;
	L2 /= 0.001;
	L3 /= 0.001;

	double thd1 = Lib_abs(_thd1)*9.549296596425384;	//convert from rad/s to RPM
	double thd2 = Lib_abs(_thd2)*9.549296596425384;
	double thd3 = Lib_abs(_thd3)*9.549296596425384;

	if(isnan(thd1)){
		this->theta_dot->p1 = 10;
	}else if(thd1 < 1){
		//this->theta_dot->p1 = 1;
	}else if(thd1 > 114){
		//this->theta_dot->p1 = 114;
	}else{
		this->theta_dot->p1 = thd1*1.2;
	}

	if(isnan(thd2)){
		this->theta_dot->p2 = 25;
	}else if(thd2 < 1){
		//this->theta_dot->p2 = 25;
	}else if(thd2 > 114){
		//this->theta_dot->p2 = 114;
	}else{
		this->theta_dot->p2 = thd2*1.4;
	}

	if(isnan(thd3)){
		this->theta_dot->p3 = 25;//15;
	}else if(thd3 < 1){
		//this->theta_dot->p3 = 25;
	}else if(thd3 > 114){
		//this->theta_dot->p3 = 114;
	}else{
		this->theta_dot->p3 = thd3;
	}

	this->setSpeedBits();
}

void Leg::setSpeedRPM(double th1d, double th2d, double th3d){
	this->theta_dot->p1 = th1d;
	this->theta_dot->p2 = th2d;
	this->theta_dot->p3 = th3d;

	this->setSpeedBits();
}

void Leg::setSpeed(double * theta_dot){
	this->theta_dot->p1 = theta_dot[0];
	this->theta_dot->p2 = theta_dot[1];
	this->theta_dot->p3 = theta_dot[2];

	this->setSpeedBits();
}
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

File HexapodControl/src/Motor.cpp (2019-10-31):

/**
 * @file Motor.cpp
 * @author Ross Christopher (CHRROS005)
 * @date
 * @brief Motor class functions.
 **/


#include "Motor.h"

Motor::Motor(uint8_t IDVal, CommsManager * comms) : ID(IDVal){
	this->comms = comms;
}

Motor::~Motor(void){

}


void Motor::setGoalPositionSpeed(double theta, double speed){
	this->calcPositionBits(theta);
	this->calcSpeedBits(speed);
}

void Motor::calcPositionBits(double theta){		//now in radians
	double pos = (theta+2.61799)*195.569883766 ; //was 150 deg and *3.41

	if(this->ID%3==0){
		pos = (theta-2.61799)*-195.569883766;
	}

	if(pos < 0){
		pos = 0;
	}else if(pos > 1023){
		pos = 1023;
	}

	this->goalMovementBits[0] = (uint16_t)pos & 0xff;
	this->goalMovementBits[1] = (uint16_t)pos >> 8;
}

void Motor::calcSpeedBits(double theta_dot){	//rpm
	double speed = theta_dot*1024.0/114.0;
	this->goalMovementBits[2] = (uint16_t)(speed < 1 ? 1 : speed) & 0xff;
	this->goalMovementBits[3] = (uint16_t)(speed < 1 ? 1 : speed) >> 8;
}

void Motor::setPositionBits(uint16_t pos){
	this->goalMovementBits[0] = (uint16_t)pos & 0xff;
	this->goalMovementBits[1] = (uint16_t)pos >> 8;
}

void Motor::setSpeedBits(uint16_t speed){
	this->goalMovementBits[2] = (uint16_t)speed & 0xff;
	this->goalMovementBits[3] = (uint16_t)speed >> 8;
}

uint8_t * Motor::getGoalMovementBits(void){
	return this->goalMovementBits;
}

void Motor::move(void){
	this->writeReg(GOAL_POSITION_L, this->goalMovementBits, 4);
}

void Motor::writeReg(enum CONTROL_TABLE reg, FunctionalState state){
	uint8_t data[1] = {state};
	this->writeReg(reg, data, 1);
}

void Motor::writeReg(enum CONTROL_TABLE reg, uint8_t * data, uint8_t dataLength){
	//write data only
	uint8_t length = dataLength + 3;

	uint8_t packet[length+4];

	packet[0] = packet[1] = 0xFF;
	packet[2] = this->ID;
	packet[3] = length;
	packet[4] = WRITE_DATA;
	packet[5] = reg;

	for(int j = 0; j < dataLength; j++){
		packet[6+j] = data[j];
	}

	packet[length+3] = 0;
	for(int i = 2; i < length+3; i++){
		packet[length+3] += packet[i];
	}

	packet[length+3] = ~packet[length+3];

	//HAL_Delay(2);			//without this DMA transmission and reception of data doesn't work...

	HAL_GPIO_WritePin(GPIOD,GPIO_PIN_12,GPIO_PIN_SET);

	comms->transmitMotors(packet, length+4, 100, BLOCKING);
}

bool Motor::readReg(enum CONTROL_TABLE reg, uint8_t dataLength){
	//this->reading = true;
	if(this->readPacket[2] != this->ID){
		this->readDataSize = dataLength;
		//read data only
		uint8_t length = 4;

		readPacket[0] = readPacket[1] = 0xFF;
		readPacket[2] = this->ID;
		readPacket[3] = length;
		readPacket[4] = READ_DATA;
		readPacket[5] = reg;

		readPacket[6] = dataLength;

		readPacket[length+3] = 0;
		for(int i = 2; i < length+3; i++){
			readPacket[length+3] += readPacket[i];
		}

		readPacket[length+3] = ~readPacket[length+3];
	}

	HAL_GPIO_WritePin(GPIOD,GPIO_PIN_12,GPIO_PIN_SET);
	for(int i = 0; i < 100000; i++);
	if(comms->transmitMotors(readPacket, 4+4, 0, DMA) == HAL_OK){
		if(comms->receiveMotors(this->controlTable,this->readDataSize+6,0,DMA) == HAL_OK){
			return true;
		}else{
			return false;
		}
	}else{
		HAL_UART_DMAStop(comms->getMotorUART());
		return false;
	}

	//for(int i = 0; i < 100000; i++);

}

bool Motor::readTable(){
	//this->reading = true;
	if(this->readPacket[2] != this->ID){
		uint8_t dataLength = 50;
		enum CONTROL_TABLE reg = MODEL_NUMBER_L;

		this->readDataSize = dataLength;
		//read data only
		uint8_t length = 4;

		readPacket[0] = readPacket[1] = 0xFF;
		readPacket[2] = this->ID;
		readPacket[3] = length;
		readPacket[4] = READ_DATA;
		readPacket[5] = reg;

		readPacket[6] = dataLength;

		readPacket[length+3] = 0;
		for(int i = 2; i < length+3; i++){
			readPacket[length+3] += readPacket[i];
		}

		readPacket[length+3] = ~readPacket[length+3];
	}

	HAL_GPIO_WritePin(GPIOD,GPIO_PIN_12,GPIO_PIN_SET);
	if(comms->transmitMotors(readPacket, 4+4, 100, BLOCKING) == HAL_OK){
		HAL_GPIO_WritePin(GPIOD,GPIO_PIN_12,GPIO_PIN_RESET);
		if(comms->receiveMotors(this->controlTable,this->readDataSize+6,1000, BLOCKING) == HAL_OK){
			return true;
		}else{
			return false;
		}
	}else{
		return false;
	}
}

void Motor::clearControlTable(){
	for(int i = 0; i < 56; i++){
		this->controlTable[i] = 0;
	}
}

void Motor::resetErrors(){
	uint8_t data[] = {255,3};
	this->writeReg(TORQUE_LIMIT_L, data, 2);

	uint8_t data2[] = {0,0};
	this->writeReg(TORQUE_ENABLE, data2, 2);

	for(int i = 0; i < 100000;i++);	//delay (HAL_Delay causes timer issues)

	uint8_t data3[] = {1,0};
	this->writeReg(TORQUE_ENABLE, data3, 2);

	for(int i = 0; i < 100000;i++);	//delay (HAL_Delay causes timer issues)
}

bool Motor::pingBool(){
	uint8_t packet[2+4];

	packet[0] = packet[1] = 0xFF;
	packet[2] = this->ID;
	packet[3] = 2;
	packet[4] = PING;


	packet[2+3] = 0;
	for(int i = 2; i < 2+3; i++){
		packet[2+3] += packet[i];
	}

	packet[2+3] = ~packet[2+3];

	HAL_GPIO_WritePin(GPIOD, GPIO_PIN_12, GPIO_PIN_SET);
	comms->transmitMotors(packet,sizeof(packet)/sizeof(packet[0]), 100, BLOCKING);
	HAL_GPIO_WritePin(GPIOD, GPIO_PIN_12, GPIO_PIN_RESET);
	comms->receiveMotors(this->pingStatusPacket, 6, 100, BLOCKING);

	return (this->pingStatusPacket[2] == this->ID);

}

uint8_t * Motor::pingData(){
	uint8_t packet[2+4];

	packet[0] = packet[1] = 0xFF;
	packet[2] = this->ID;
	packet[3] = 2;
	packet[4] = PING;


	packet[2+3] = 0;
	for(int i = 2; i < 2+3; i++){
		packet[2+3] += packet[i];
	}

	packet[2+3] = ~packet[2+3];

	HAL_GPIO_WritePin(GPIOD, GPIO_PIN_12, GPIO_PIN_SET);
	comms->transmitMotors(packet, sizeof(packet)/sizeof(packet[0]), 100, BLOCKING);
	HAL_GPIO_WritePin(GPIOD, GPIO_PIN_12, GPIO_PIN_RESET);
	if(comms->receiveMotors(this->pingStatusPacket, 6, 100, BLOCKING)==HAL_TIMEOUT){
		this->pingStatusPacket[2] = 0;
	}

	return this->pingStatusPacket;

}

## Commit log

2019-11-05 Update Leg.cpp
    fixed speed equations th1d th2d th3d
    [Leg.cpp]
2019-11-20 removed 3d printed foot
    [Assembly-Leg_no_foot.SLDASM, Leg - Tibia - machined_no_foot.SLDPRT]
